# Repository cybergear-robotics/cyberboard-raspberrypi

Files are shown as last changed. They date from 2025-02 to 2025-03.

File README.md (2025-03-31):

# CyberBoard - Raspberry PI 4




This is the Kicad project for the CyberBoard Raspberry PI HAT. It has an ESP32S3 which is
connected via UART to the Raspberry PI. The microcontroller drives the cybergear 
motors via CAN. Furthermore a MOLEX CLIK connector is integrated in order
to communicate with the power distribution board [Holybro PM03D Pixhawk 5X Power
Module](https://docs.holybro.com/power-module-and-pdb/power-module/digital-power-module-pm-setup).

## Features

* 5V power supply connectior compatible with **Holybro PM03D Pixhawk** with
  support for the INA226 power monitor unit.
* ESP32S3 with dual-core CPU.
* CAN transceiver TJA1051T for communication with **Xiaomi CyberGears**.
* 5V fan connector for Raspberry PI with support for `gpio-fan` (PWM).
* Connector for external WS2812B LEDs.
* Connector 4x GPIO including 3.3V and 5V supply.
* Conenctor for lidar sensors from Slamtec (tested with RPLIDAR A3).
* 2x UART communication lines between ESP32S3 and Raspberry PI.
  * Serial log for debugging purposes, flashing and burning fuse-bits.
  * **ROS2 Serial Agent** communication
* **JTAG** connection between ESP32S3 and Raspberry PI
* Connector for external switch/button with LED support.

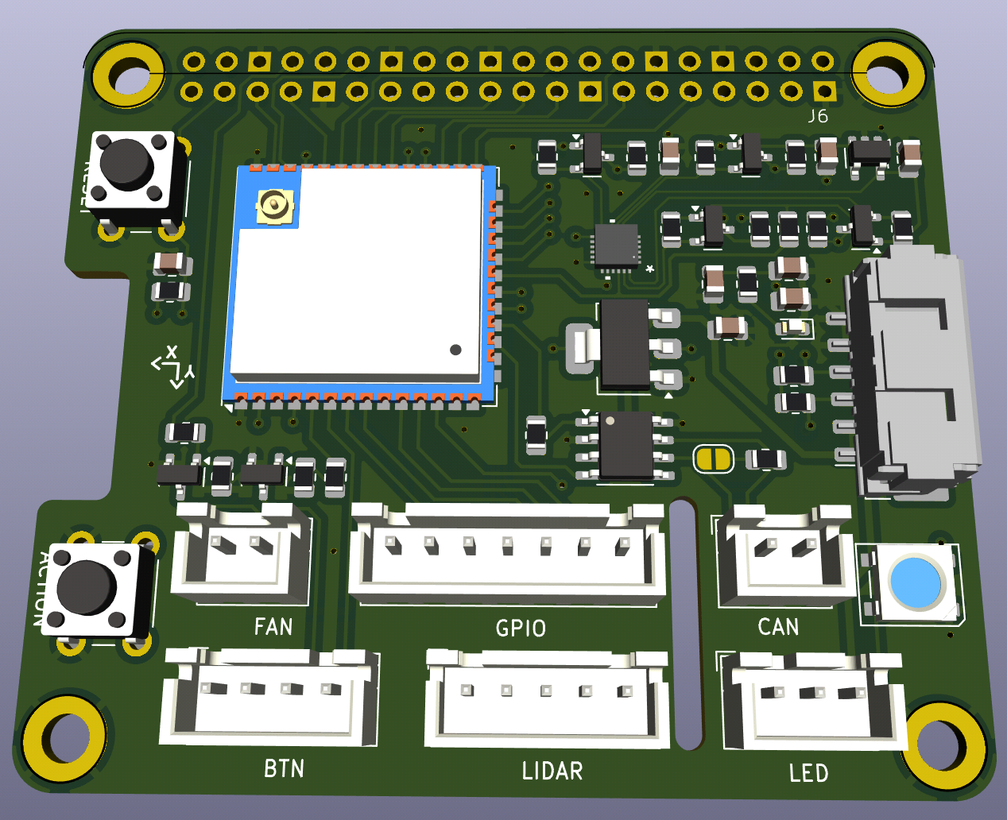
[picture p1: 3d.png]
3D

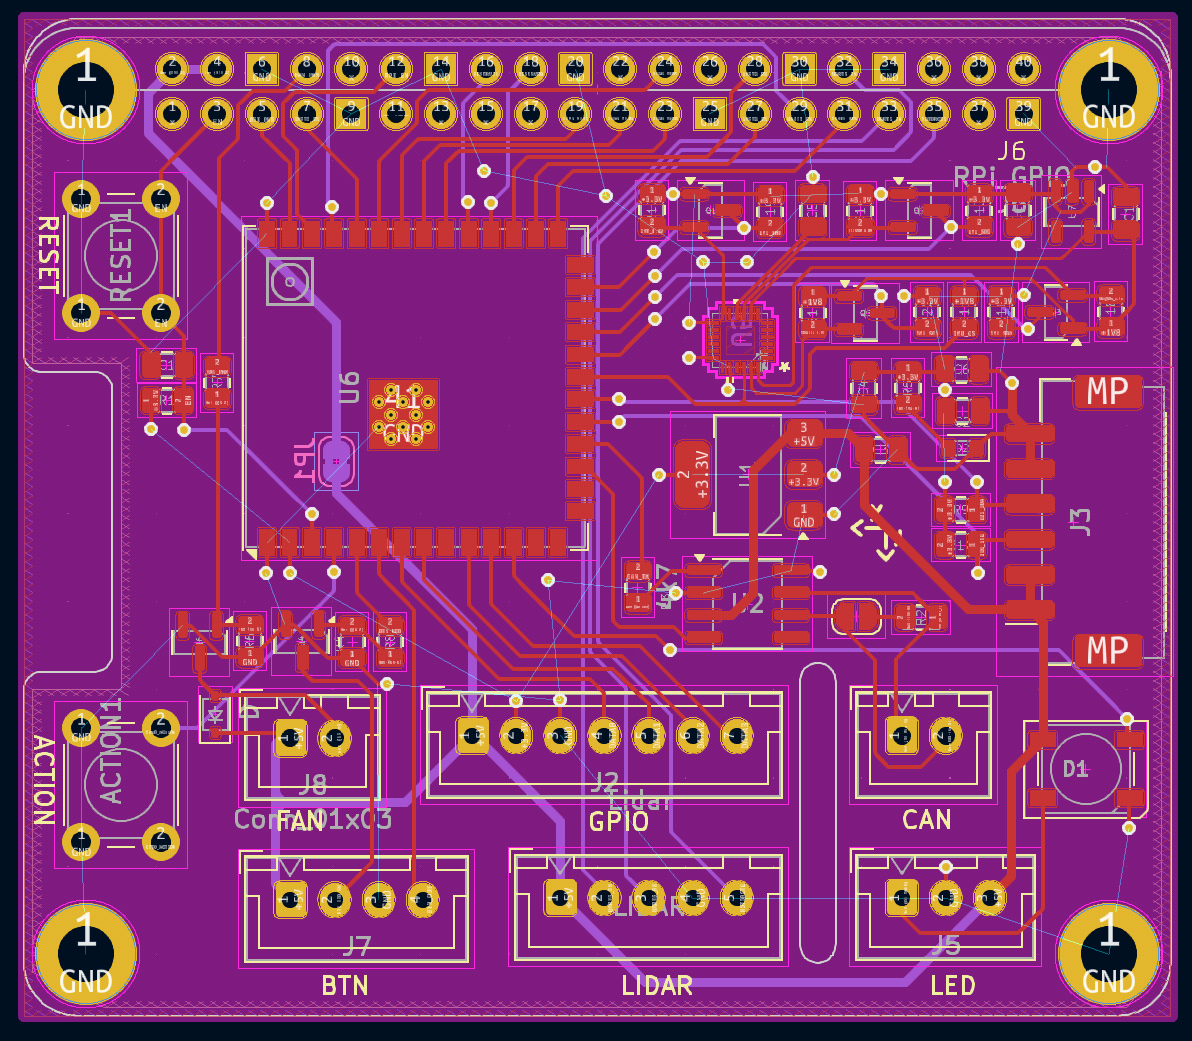
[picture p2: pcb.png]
PCB


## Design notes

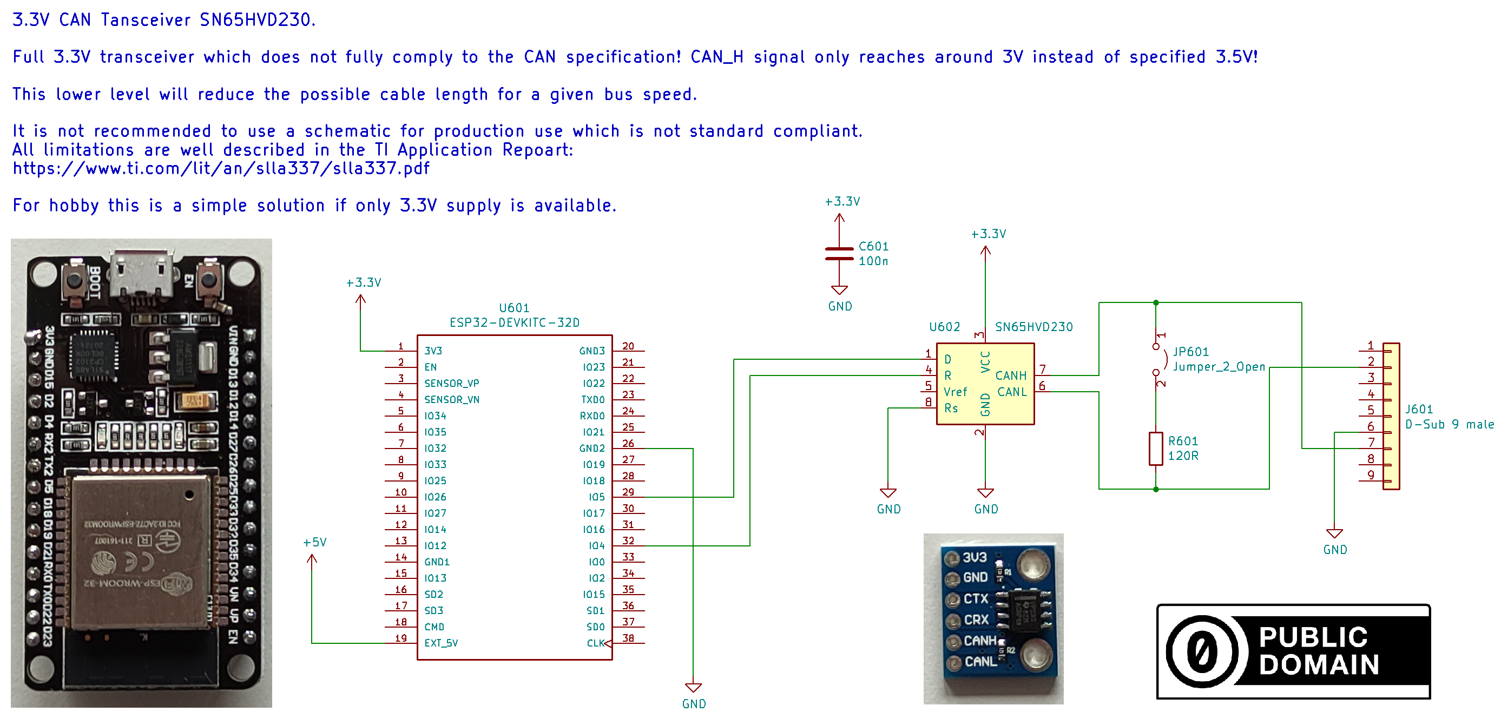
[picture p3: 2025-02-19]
datasheets/canbus_esp32_3v3.png

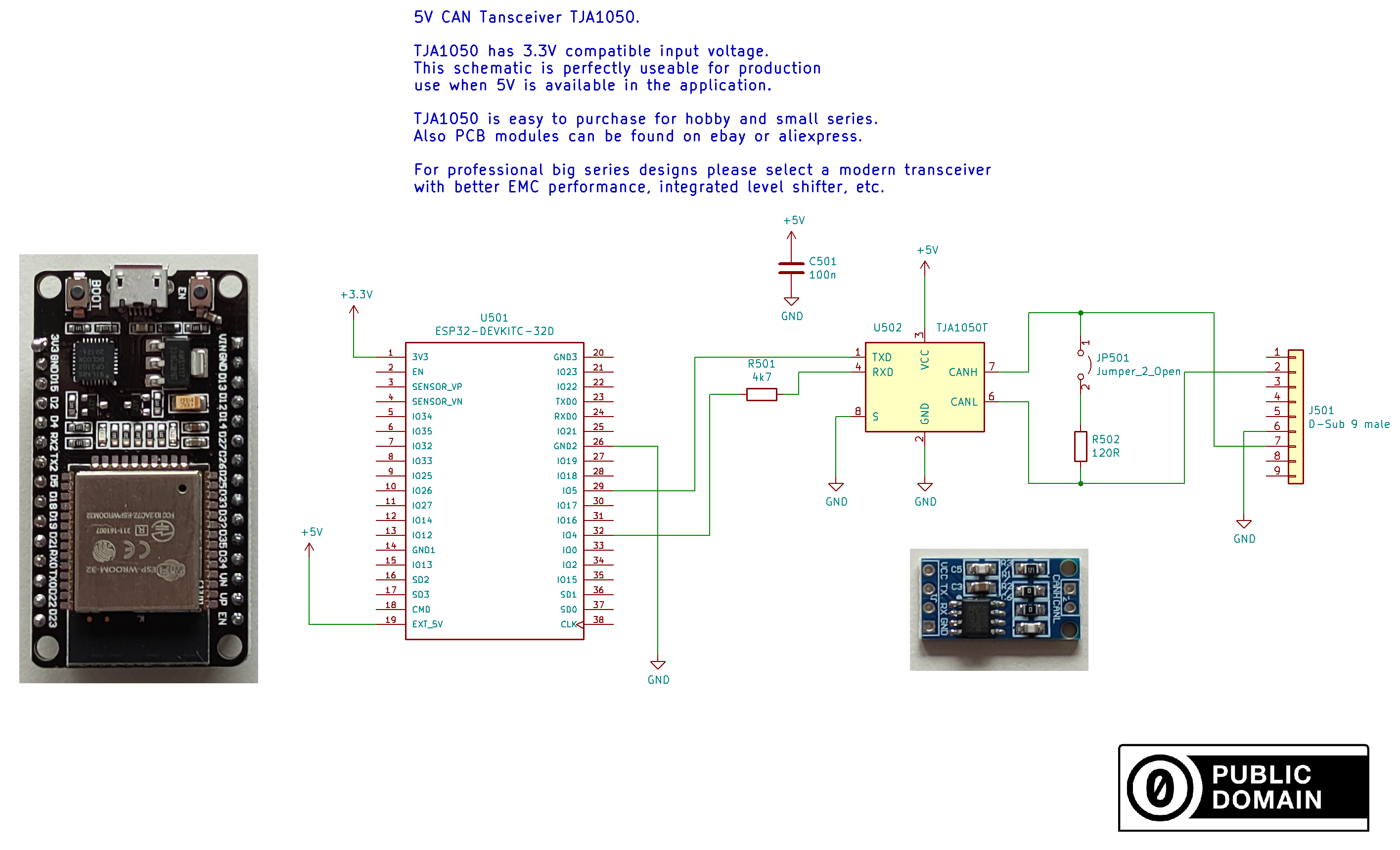
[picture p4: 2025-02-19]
datasheets/canbus_esp32_5v.png

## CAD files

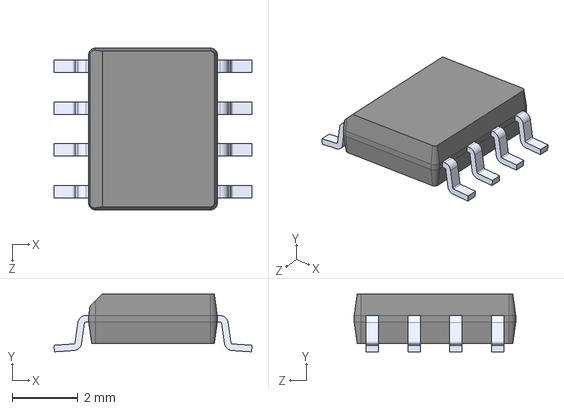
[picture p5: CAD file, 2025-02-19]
3dmodels/TJA1050T_CM_118.step
6.00 x 1.75 x 4.90 mm

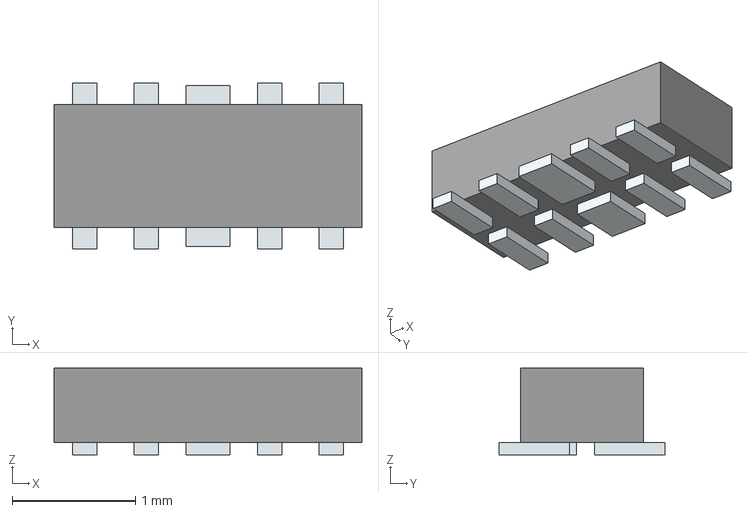
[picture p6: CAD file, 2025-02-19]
3dmodels/3D_MODEL_D3V3XA4B10LP-7.stp
2.50 x 1.35 x 0.705 mm
Pins

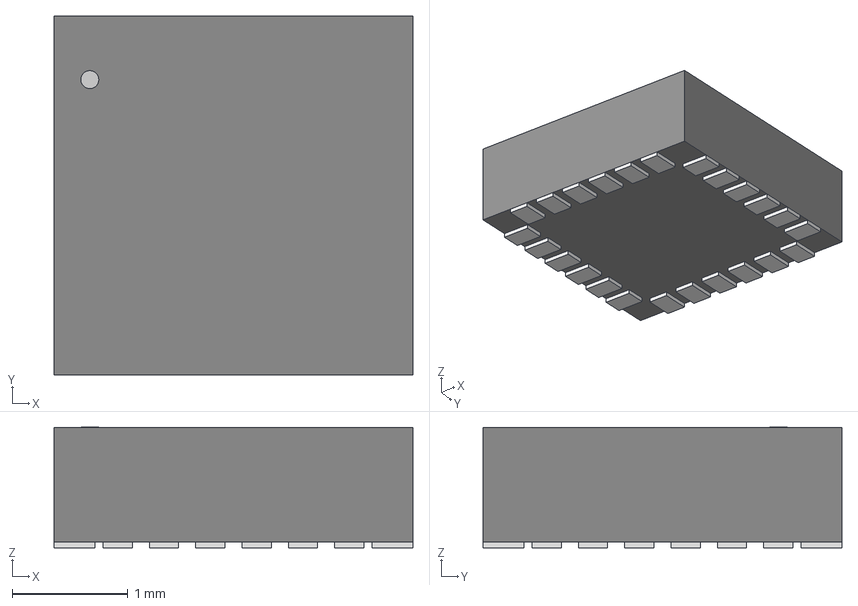
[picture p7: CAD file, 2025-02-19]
3dmodels/QFN24_3X3X0P9_IVS.step
3.10 x 3.10 x 1.04 mm

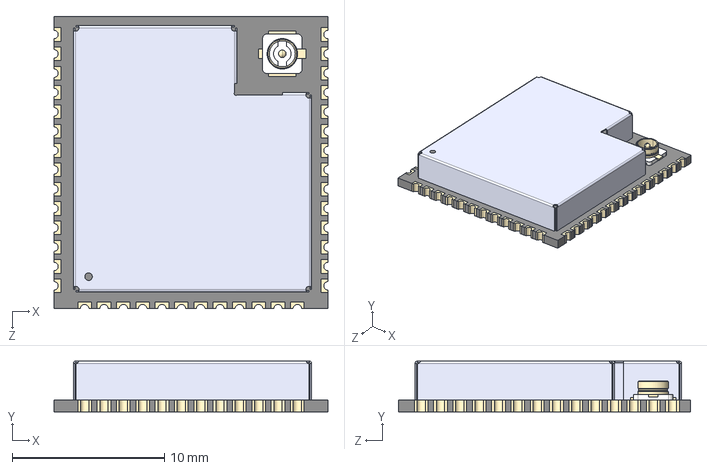
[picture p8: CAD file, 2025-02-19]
3dmodels/ESP32-S3-WROOM-1U-N4.STEP
18.0 x 3.35 x 19.2 mm

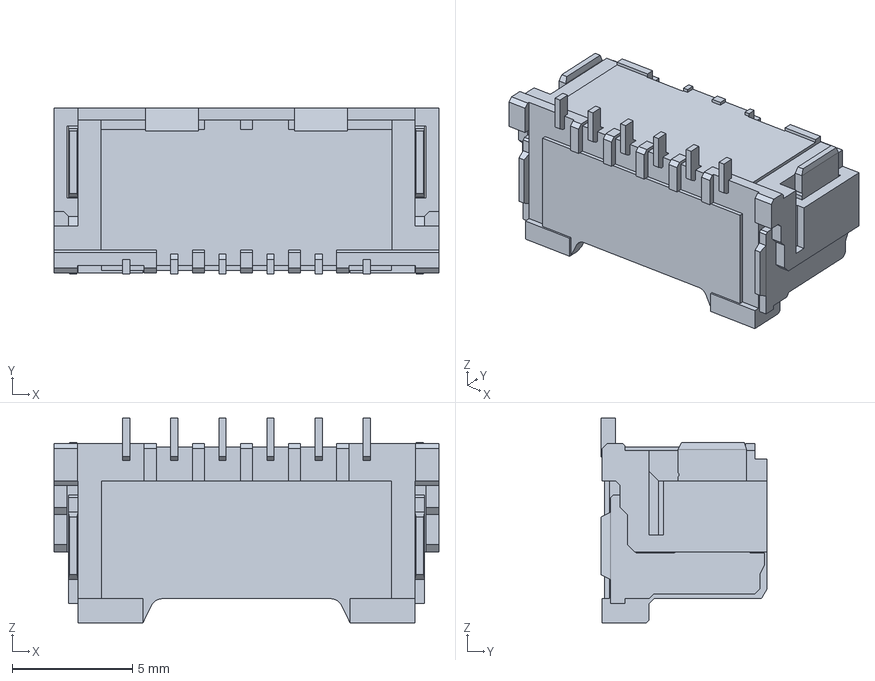
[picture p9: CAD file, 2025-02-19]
3dmodels/5024940670.stp
16.0 x 6.90 x 8.50 mm

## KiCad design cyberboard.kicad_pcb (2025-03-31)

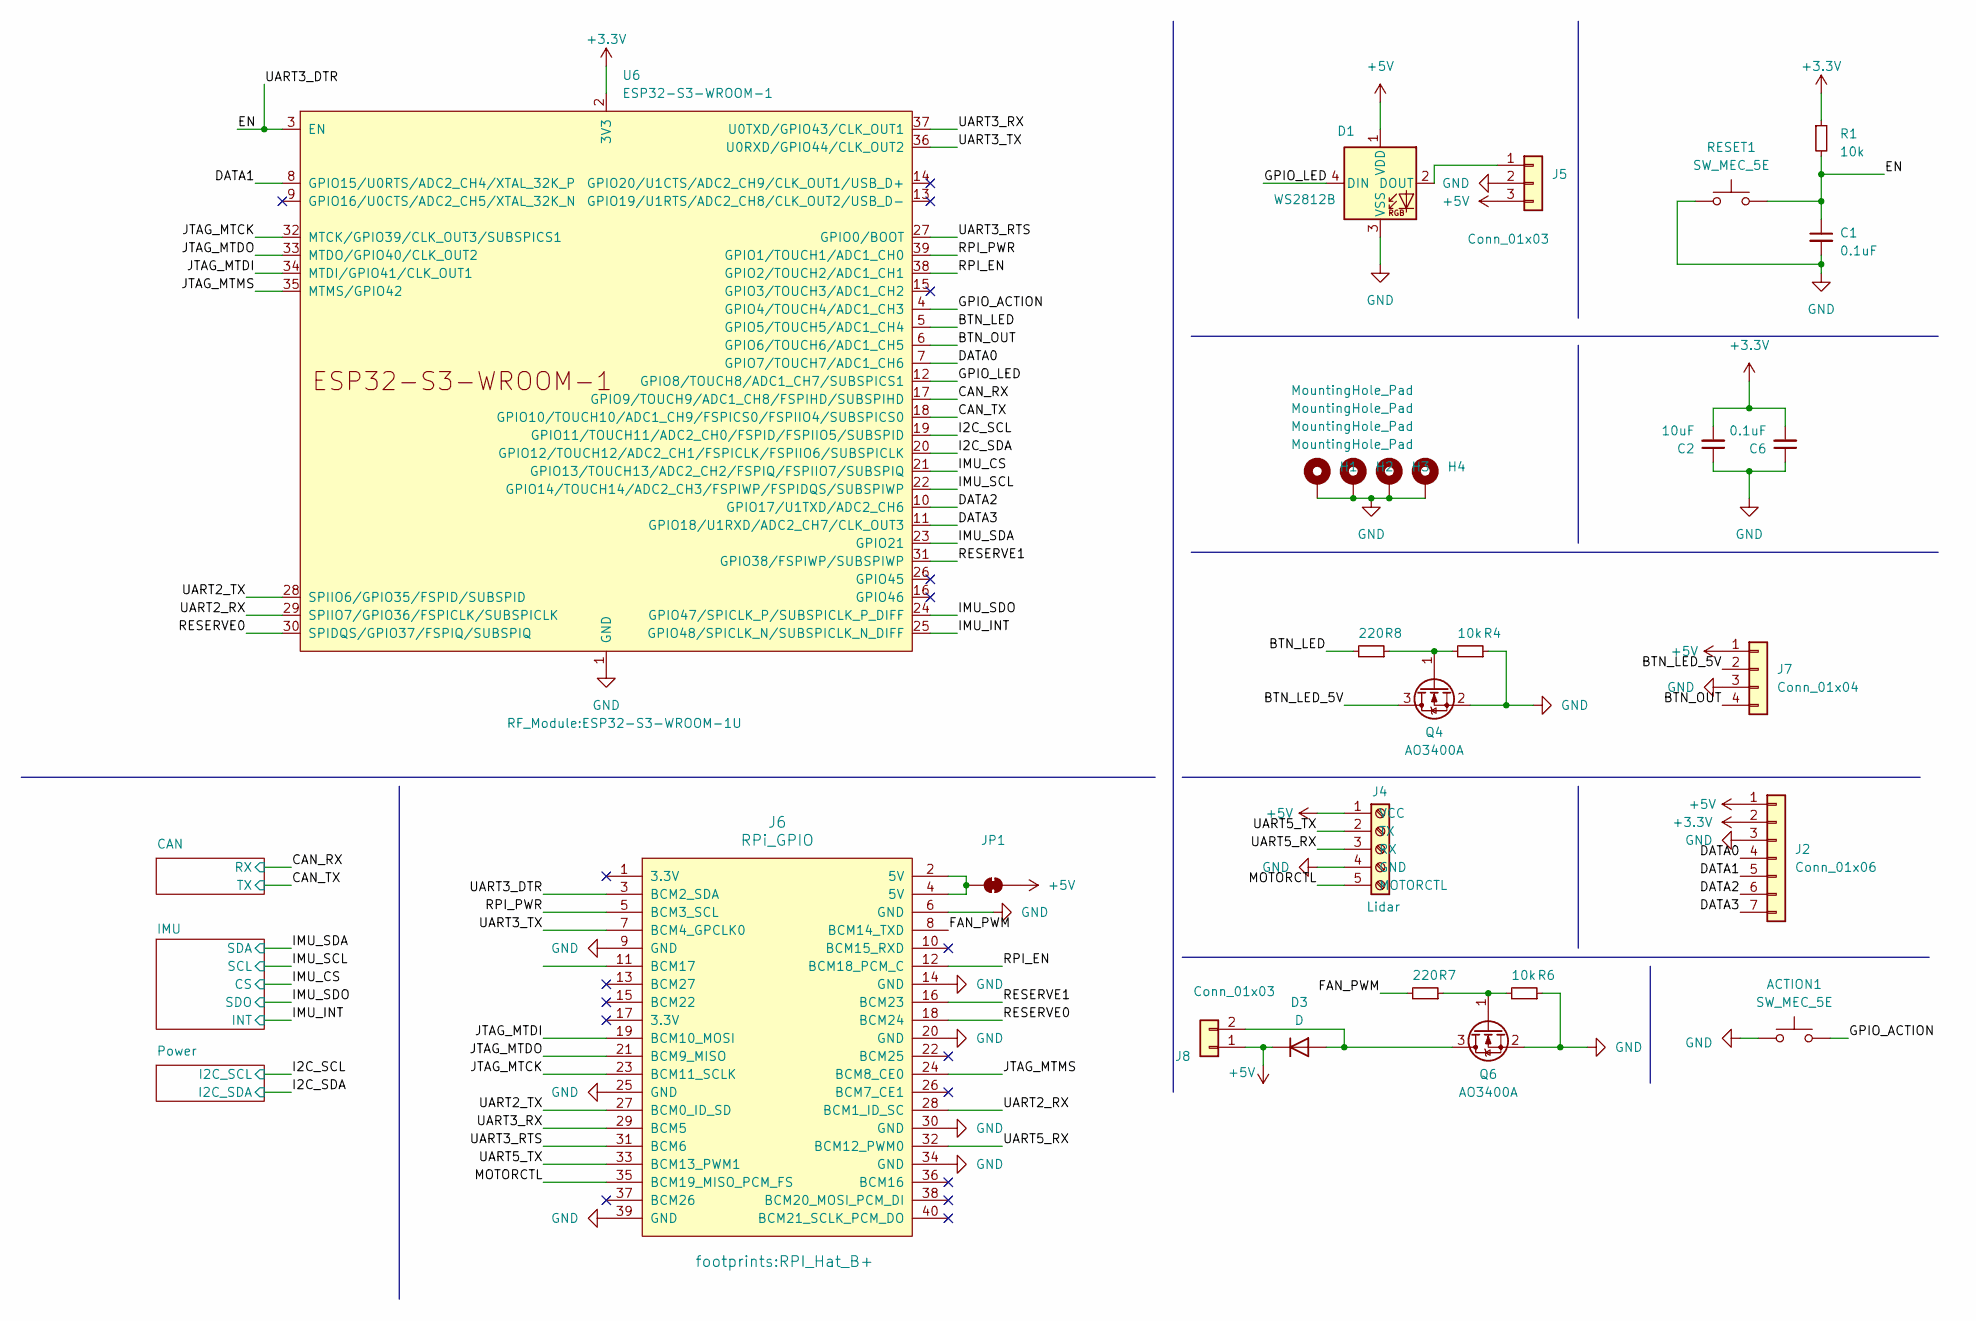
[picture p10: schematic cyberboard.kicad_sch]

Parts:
ACTION1: SW_MEC_5E; SW_PUSH_6mm_H5mm; LCSC C318884
C1, C6: 0.1uF; C_0805_2012Metric; LCSC C49678
C2: 10uF; C_0805_2012Metric; LCSC C15850
D1: WS2812B; LED_WS2812B_PLCC4_5.0x5.0mm_P3.2mm
D3: D; D_SOD-323; LCSC C191023
H1, H2, H3, H4: MountingHole_Pad; MountingHole_3.2mm_M3_DIN965_Pad
J2: Conn_01x06; JST_XH_B7B-XH-A_1x07_P2.50mm_Vertical
J4: Lidar; JST_XH_B5B-XH-A_1x05_P2.50mm_Vertical
J5: Conn_01x03; JST_XH_B3B-XH-A_1x03_P2.50mm_Vertical
J6: RPi_GPIO; RPI_Hat_B+
J7: Conn_01x04; JST_XH_B4B-XH-A_1x04_P2.50mm_Vertical
J8: Conn_01x03; JST_XH_B2B-XH-A_1x02_P2.50mm_Vertical
JP1: SolderJumper_2_Open; SolderJumper-2_P1.3mm_Bridged2Bar_RoundedPad1.0x1.5mm
Q4, Q6: AO3400A; SOT-23; LCSC C20917
R1, R4, R6: 10k; R_0805_2012Metric; LCSC C17414
R7, R8: 220; R_0805_2012Metric; LCSC C17557
RESET1: SW_MEC_5E; SW_PUSH_6mm_H5mm; LCSC C318884
U6: ESP32-S3-WROOM-1; ESP32-S3-WROOM-1U

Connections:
+3.3V: C2.2, C6.2, J2.2, R1.1, U6.2 (3V3); also elsewhere on the board
+5V: D1.1 (VDD), D3.1 (K), J2.1, J4.1 (VCC), J5.3, J7.1, J8.1, JP1.2 (B); also elsewhere on the board
/BTN_LED: R8.2, U6.5 (GPIO5/TOUCH5/ADC1_CH4)
/BTN_LED_5V: J7.2, Q4.3 (D)
/BTN_OUT: J7.4, U6.6 (GPIO6/TOUCH6/ADC1_CH5)
/CAN_RX: U6.17 (GPIO9/TOUCH9/ADC1_CH8/FSPIHD/SUBSPIHD); also elsewhere on the board
/CAN_TX: U6.18 (GPIO10/TOUCH10/ADC1_CH9/FSPICS0/FSPIIO4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); also elsewhere on the board
/DATA0: J2.4, U6.7 (GPIO7/TOUCH7/ADC1_CH6)
/DATA1: J2.5, U6.8 (GPIO15/U0RTS/ADC2_CH4/XTAL_32K_P)
/DATA2: J2.6, U6.10 (GPIO17/U1TXD/ADC2_CH6)
/DATA3: J2.7, U6.11 (GPIO18/U1RXD/ADC2_CH7/CLK_OUT3)
/EN: C1.1, J6.3 (BCM2_SDA), R1.2, RESET1.2, U6.3 (EN)
/FAN_PWM: J6.8 (BCM14_TXD), R7.2
/GPIO_ACTION: ACTION1.2, U6.4 (GPIO4/TOUCH4/ADC1_CH3)
/GPIO_LED: D1.4 (DIN), U6.12 (GPIO8/TOUCH8/ADC1_CH7/SUBSPICS1)
/I2C_SCL: U6.19 (GPIO11/TOUCH11/ADC2_CH0/FSPID/FSPIIO5/S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); also elsewhere on the board
/I2C_SDA: U6.20 (GPIO12/TOUCH12/ADC2_CH1/FSPICLK/FSPIIO6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); also elsewhere on the board
/IMU_CS: U6.21 (GPIO13/TOUCH13/ADC2_CH2/FSPIQ/FSPIIO7/S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); also elsewhere on the board
/IMU_INT: U6.25 (GPIO48/SPICLK_N/SUBSPICLK_N_DIFF); also elsewhere on the board
/IMU_SCL: U6.22 (GPIO14/TOUCH14/ADC2_CH3/FSPIWP/FSPIDQS/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); also elsewhere on the board
/IMU_SDA: U6.23 (GPIO21); also elsewhere on the board
/IMU_SDO: U6.24 (GPIO47/SPICLK_P/SUBSPICLK_P_DIFF); also elsewhere on the board
/JTAG_MTCK: J6.23 (BCM11_SCLK), U6.32 (MTCK/GPIO39/CLK_OUT3/SUBSPICS1)
/JTAG_MTDI: J6.19 (BCM10_MOSI), U6.34 (MTDI/GPIO41/CLK_OUT1)
/JTAG_MTDO: J6.21 (BCM9_MISO), U6.33 (MTDO/GPIO40/CLK_OUT2)
/JTAG_MTMS: J6.24 (BCM8_CE0), U6.35 (MTMS/GPIO42)
/MOTORCTL: J4.5 (MOTORCTL), J6.35 (BCM19_MISO_PCM_FS)
/RESERVE0: J6.18 (BCM24), U6.30 (SPIDQS/GPIO37/FSPIQ/SUBSPIQ)
/RESERVE1: J6.16 (BCM23), U6.31 (GPIO38/FSPIWP/SUBSPIWP)
/RPI_EN: J6.12 (BCM18_PCM_C), U6.38 (GPIO2/TOUCH2/ADC1_CH1)
/RPI_PWR: J6.5 (BCM3_SCL), U6.39 (GPIO1/TOUCH1/ADC1_CH0)
/UART2_RX: J6.28 (BCM1_ID_SC), U6.29 (SPIIO7/GPIO36/FSPICLK/SUBSPICLK)
/UART2_TX: J6.27 (BCM0_ID_SD), U6.28 (SPIIO6/GPIO35/FSPID/SUBSPID)
/UART3_RTS: J6.31 (BCM6), U6.27 (GPIO0/BOOT)
/UART3_RX: J6.29 (BCM5), U6.37 (U0TXD/GPIO43/CLK_OUT1)
/UART3_TX: J6.7 (BCM4_GPCLK0), U6.36 (U0RXD/GPIO44/CLK_OUT2)
/UART5_RX: J4.3 (RX), J6.32 (BCM12_PWM0)
/UART5_TX: J4.2 (TX), J6.33 (BCM13_PWM1)
GND: ACTION1.1, C1.2, C2.1, C6.1, D1.3 (VSS), H1.1, H2.1, H3.1, H4.1, J2.3, J4.4 (GND), J5.2, J6.6 (GND), J6.9 (GND), J6.14 (GND), J6.20 (GND), J6.25 (GND), J6.30 (GND), J6.34 (GND), J6.39 (GND), J7.3, Q4.2 (S), Q6.2 (S), R4.1, R6.1, RESET1.1, U6.1 (GND), U6.40 (GND), U6.41 (GND); also elsewhere on the board
unnamed: D1.2 (DOUT), J5.1
unnamed: D3.2 (A), J8.2, Q6.3 (D)
unnamed: J6.2 (5V), J6.4 (5V), JP1.1 (A)
unnamed: Q4.1 (G), R4.2, R8.1
unnamed: Q6.1 (G), R6.2, R7.1

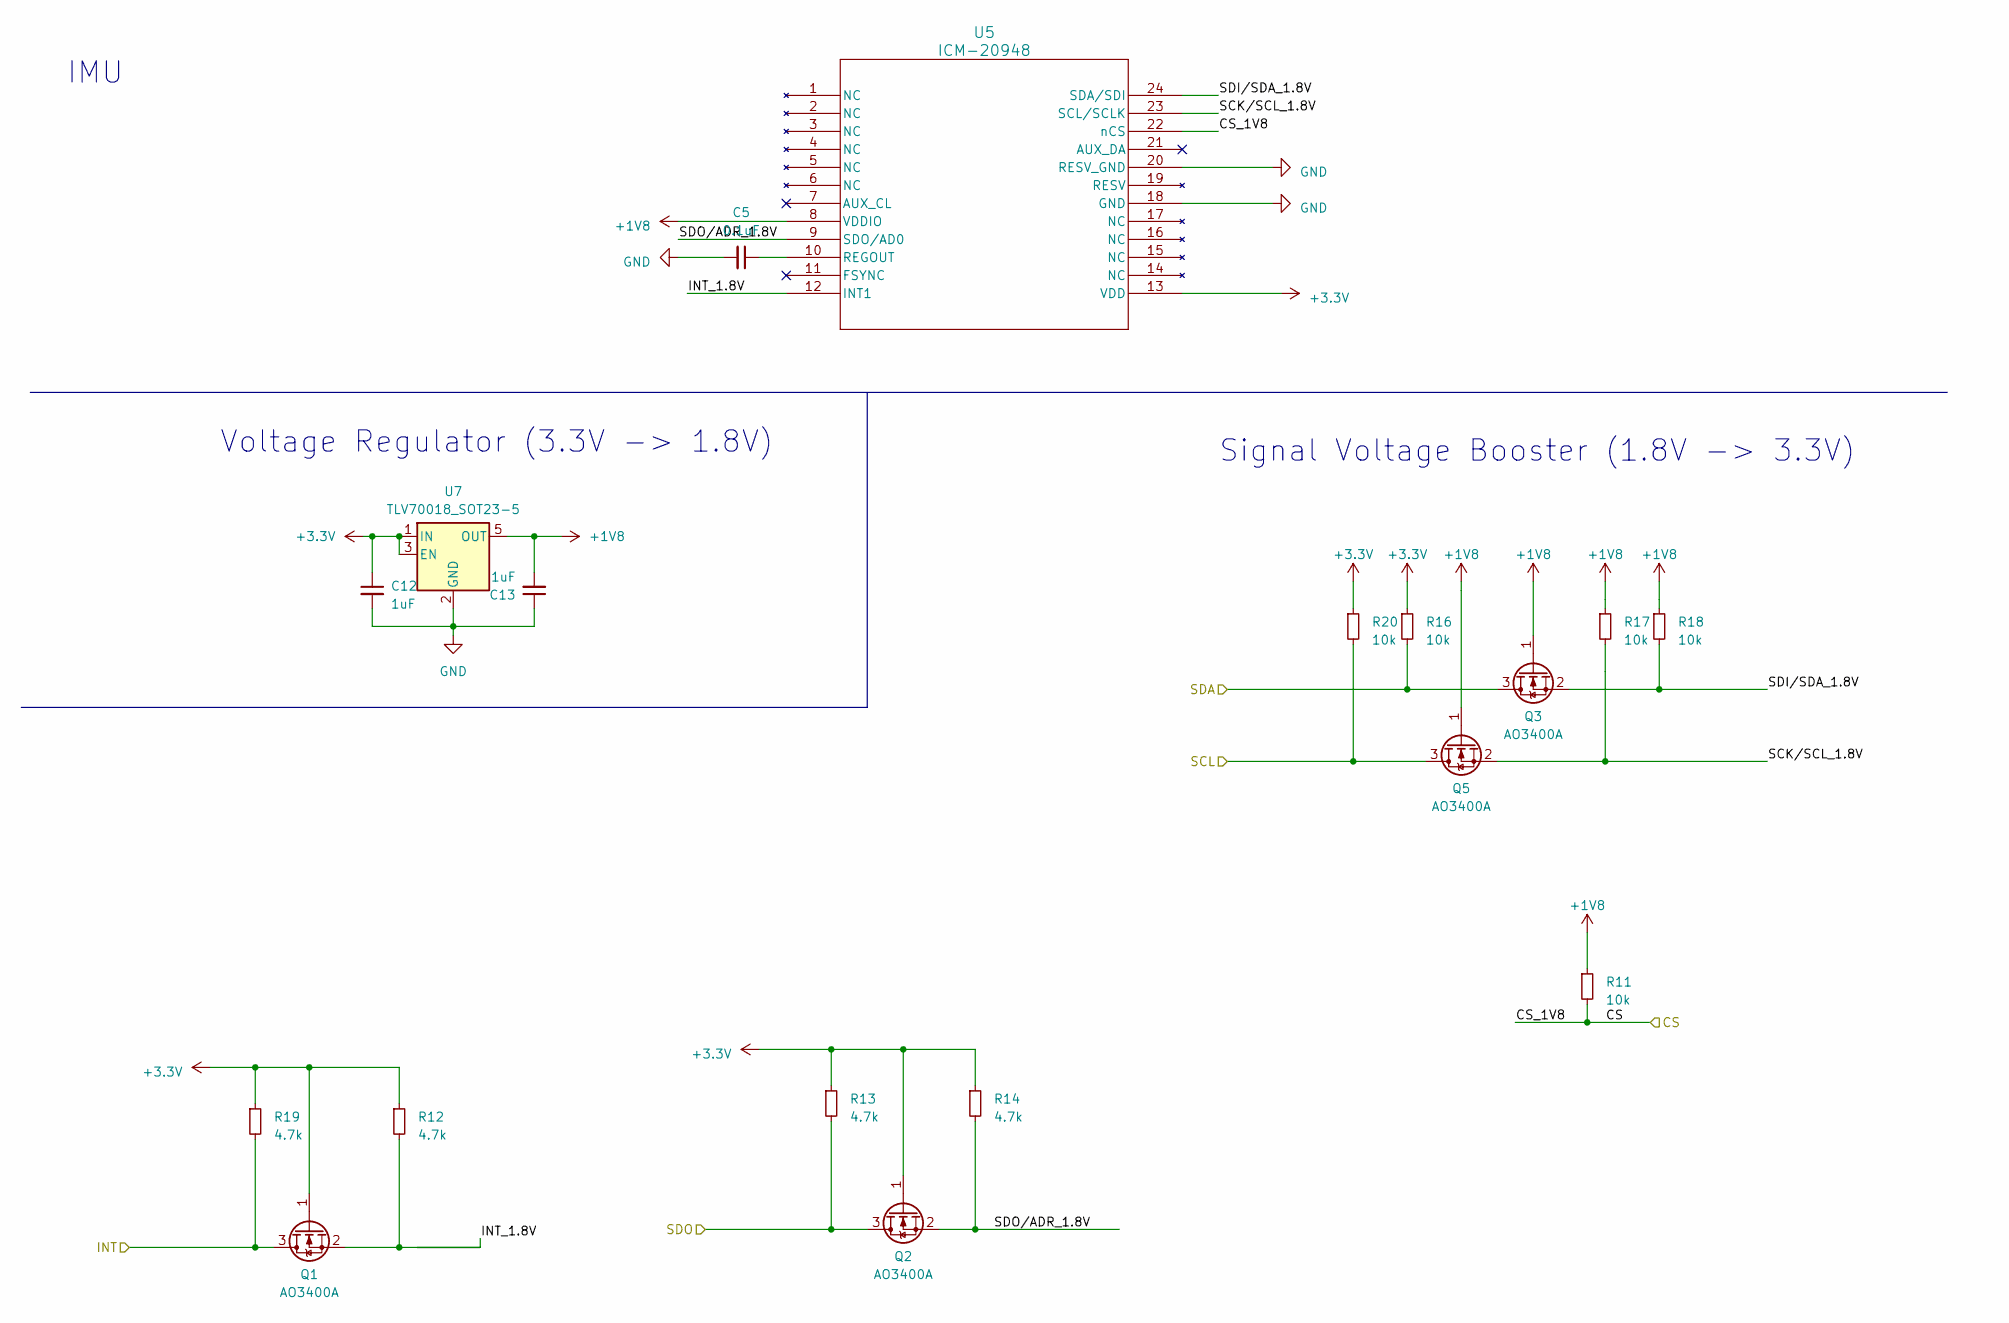
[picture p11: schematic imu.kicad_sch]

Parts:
C5: 0.1uF; C_0805_2012Metric; LCSC C49678
C12, C13: 1uF; C_0805_2012Metric; LCSC C28323
Q1, Q2, Q3, Q5: AO3400A; SOT-23; LCSC C20917
R11, R16, R17, R18, R20: 10k; R_0805_2012Metric; LCSC C17414
R12, R13, R14, R19: 4.7k; R_0805_2012Metric; LCSC C17673
U5: ICM-20948; QFN24_3X3X0P9_IVS; LCSC C726001
U7: TLV70018_SOT23-5; SOT-23-5; LCSC C79924

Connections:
+1V8: C13.2, Q3.1 (G), Q5.1 (G), R11.1, R17.1, R18.1, U5.8 (VDDIO), U7.5 (OUT)
+3.3V: C12.1, Q1.1 (G), Q2.1 (G), R12.1, R13.1, R14.1, R16.1, R19.1, R20.1, U5.13 (VDD), U7.1 (IN), U7.3 (EN); also elsewhere on the board
/IMU/INT_1.8V: Q1.2 (S), R12.2, U5.12 (INT1)
/IMU_CS: R11.2, U5.22 (nCS); also elsewhere on the board
/IMU_INT: Q1.3 (D), R19.2; also elsewhere on the board
/IMU_SCL: Q5.3 (D), R20.2; also elsewhere on the board
/IMU_SDA: Q3.3 (D), R16.2; also elsewhere on the board
/IMU_SDO: Q2.3 (D), R13.2; also elsewhere on the board
GND: C5.2, C12.2, C13.1, U5.18 (GND), U5.20 (RESV_GND), U7.2 (GND); also elsewhere on the board
unnamed: C5.1, U5.10 (REGOUT)

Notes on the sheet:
IMU
Signal Voltage Booster (1.8V -> 3.3V)
Voltage Regulator (3.3V -> 1.8V)

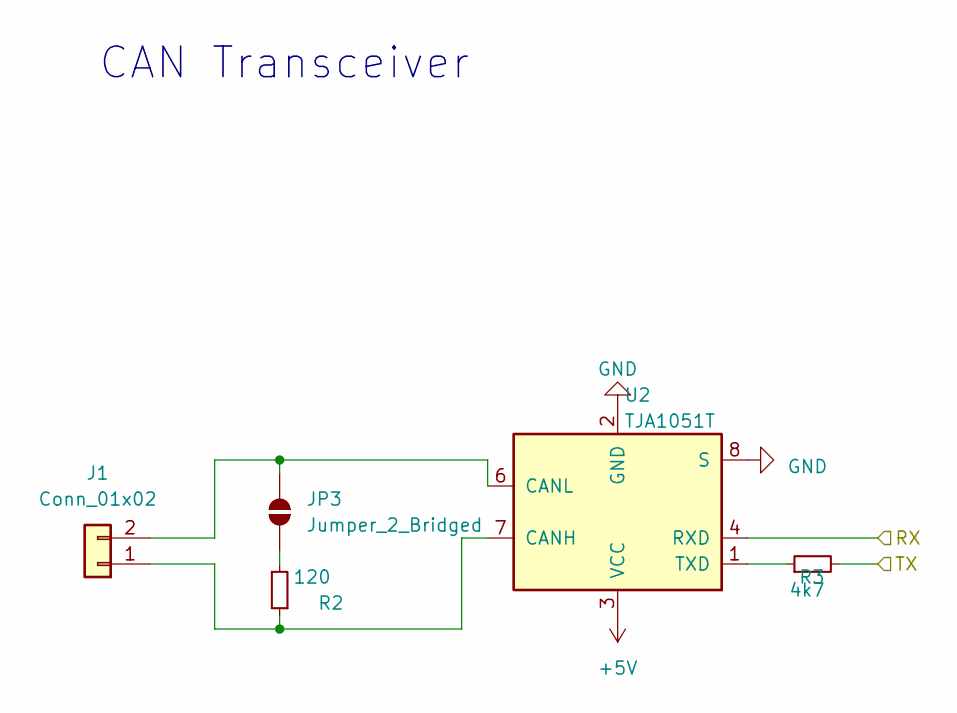
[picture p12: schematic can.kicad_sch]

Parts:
J1: Conn_01x02; JST_XH_B2B-XH-A_1x02_P2.50mm_Vertical
JP3: Jumper_2_Bridged; SolderJumper-2_P1.3mm_Open_RoundedPad1.0x1.5mm
R2: 120; R_0805_2012Metric; LCSC C17437
R3: 4k7; R_0805_2012Metric; LCSC C17673
U2: TJA1051T; SOIC-8_3.9x4.9mm_P1.27mm; LCSC C92211

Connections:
+5V: U2.3 (VCC); also elsewhere on the board
/CAN_RX: U2.4 (RXD); also elsewhere on the board
/CAN_TX: R3.2; also elsewhere on the board
GND: U2.2 (GND), U2.8 (S); also elsewhere on the board
unnamed: J1.1, R2.1, U2.7 (CANH)
unnamed: J1.2, JP3.2 (B), U2.6 (CANL)
unnamed: JP3.1 (A), R2.2
unnamed: R3.1, U2.1 (TXD)

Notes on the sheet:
CAN Transceiver

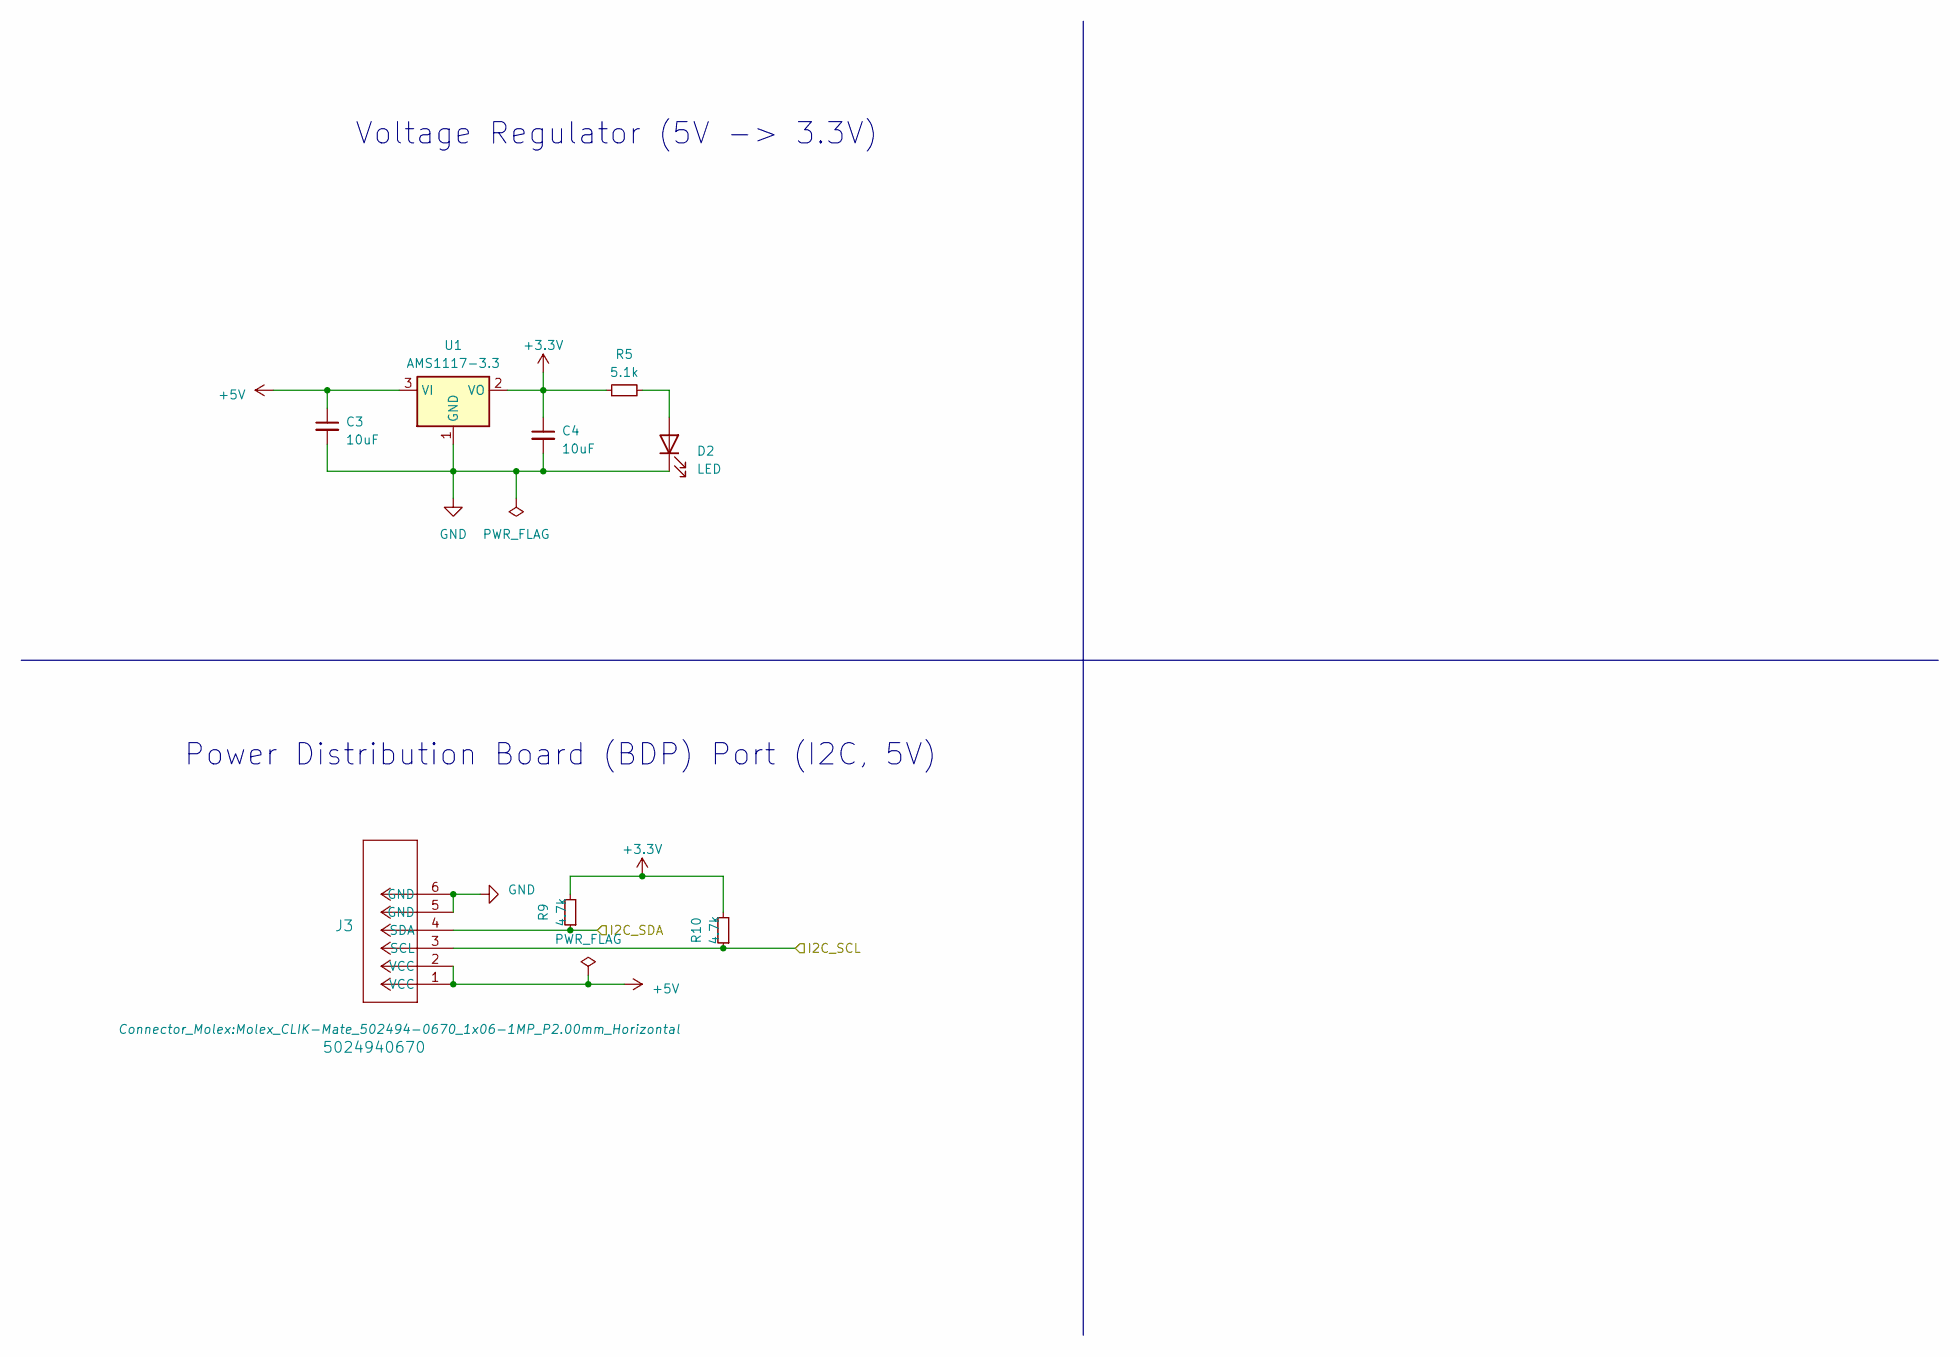
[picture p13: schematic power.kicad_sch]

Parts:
C3, C4: 10uF; C_0805_2012Metric; LCSC C15850
D2: LED; LED_0603_1608Metric; LCSC C2286
J3: 5024940670; Molex_CLIK-Mate_502494-0670_1x06-1MP_P2.00mm_Horizontal; LCSC C587930
R5: 5.1k; R_0805_2012Metric; LCSC C27834
R9, R10: 4.7k; R_0805_2012Metric; LCSC C17673
U1: AMS1117-3.3; SOT-223-3_TabPin2; LCSC C6186

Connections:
+3.3V: C4.1, R5.1, R9.2, R10.2, U1.2 (VO); also elsewhere on the board
+5V: C3.1, J3.1 (VCC), J3.2 (VCC), U1.3 (VI); also elsewhere on the board
/I2C_SCL: J3.3 (SCL), R10.1; also elsewhere on the board
/I2C_SDA: J3.4 (SDA), R9.1; also elsewhere on the board
GND: C3.2, C4.2, D2.1 (K), J3.5 (GND), J3.6 (GND), U1.1 (GND); also elsewhere on the board
unnamed: D2.2 (A), R5.2

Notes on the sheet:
Voltage Regulator (5V -> 3.3V)
Power Distribution Board (BDP) Port (I2C, 5V)

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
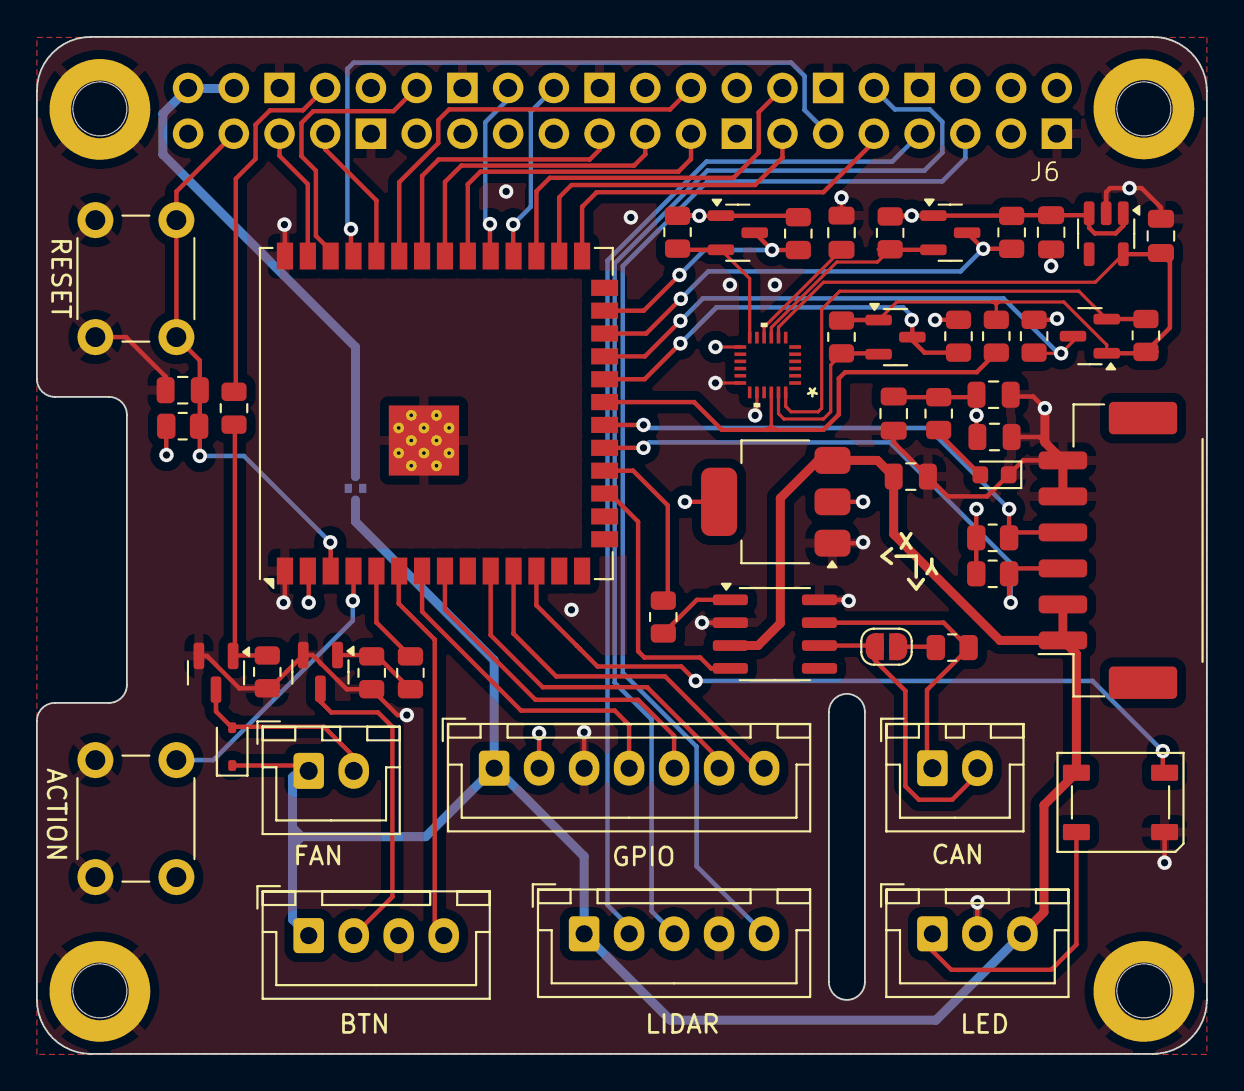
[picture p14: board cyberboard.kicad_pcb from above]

Board: 4 copper layers, 65.0 x 56.5 mm, 57 parts (1 on the bottom side), 55 nets.

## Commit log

2025-02-19 inital commit with pcb for RPi
    [3D_MODEL_D3V3XA4B10LP-7.stp, 5024940670.stp, ESP32-S3-WROOM-1U-N4.STEP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]
2025-03-15 fix bugs
    [cyberboard.kicad_pcb, cyberboard.kicad_sch, power.kicad_sch]
2025-03-30 fix BTN mosfet connection
    [cyberboard.kicad_pcb, cyberboard.kicad_sch]
2025-03-30 swap CAN TX/RX
    [can.kicad_sch, cyberboard.kicad_pcb, cyberboard.kicad_sch]
2025-03-30 swap CAN TX/RX at JST connector
    [can.kicad_sch, cyberboard.kicad_pcb]
2025-03-31 add LED connector and update FAN connector
    [cyberboard.kicad_pcb, cyberboard.kicad_sch]
2025-03-31 add missing part numbers for JLCPCB
    [cyberboard.kicad_sch]
2025-03-31 fix pcb layout
    [cyberboard.kicad_pcb, cyberboard.kicad_sch]

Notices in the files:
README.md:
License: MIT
